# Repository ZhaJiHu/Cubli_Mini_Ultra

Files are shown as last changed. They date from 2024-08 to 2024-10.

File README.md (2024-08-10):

# Cubli_Mini_Ultra项目

**项目完全开源，任何人都可以根据本Github内容自行白嫖，当然也可以顺手点个Star**

## **责任声明：本项目飞轮峰值转速可达到6500RPM，具有一定的危险性，复刻本项目的同学如若发生任何意外，与本人无关**

### 介绍

本项目在Cubli_mini的基础上加上主动刹车，缩小体积。可自动起跳，实现边和点平衡。Cubli_Mini是一个8x8x8CM的立方体，主控集成3路电机驱动、控制、无线射频一体。增加了每个飞轮的外围一圈光污染，主控也增加一条光污染。

项目成本：≤1040RMB

**视频介绍：**[https://www.bilibili.com/video/BV1Gi421D7bc/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](https://www.bilibili.com/video/BV1Gi421D7bc/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)

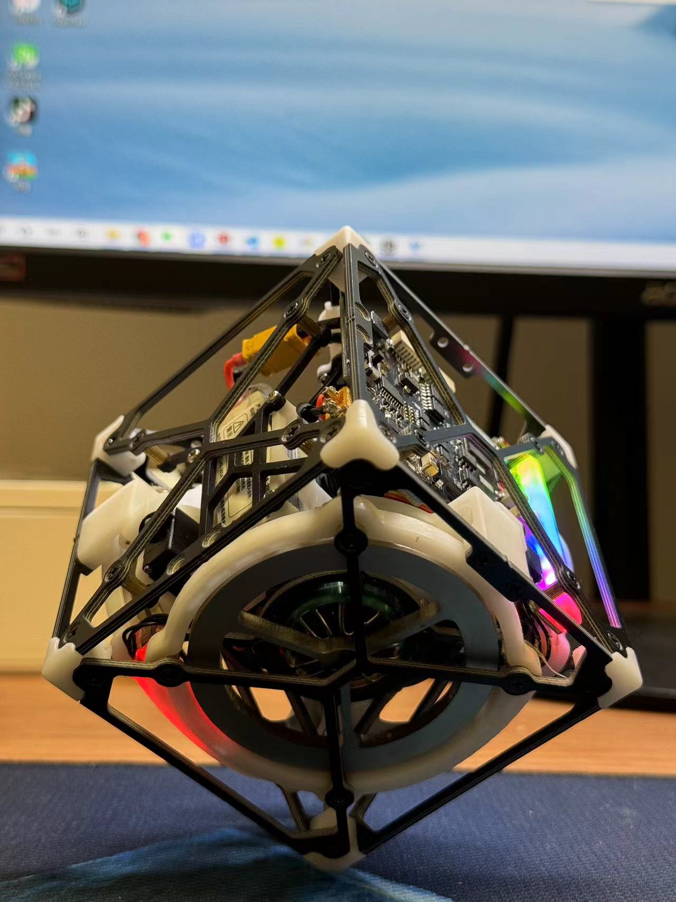
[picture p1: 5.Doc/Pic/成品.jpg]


### 资料说明

- 3D模型设计源文件
- 主控模块、IMU模块、编码器模块、下载模块硬件资料
  - BOM
  - 原理图
  - 位号图
  - Gerber
- 主控1、主控2软件工程
  - 主控模块使用两颗ESP32
- 串口调试助手&简易调参上位机
  - 串口
  - WIFI
- 各类文档说明
  - 对项目的一些说明，如调参，控制原理等
- 打样文件
  - STL格式3D打印文件
  - DWG格式钣金文件
  - BOM表
    - 结构BOM表
    - PCB元器件BOM表

### 结构设计

- 优化了角的结构件设计，通用

- 电池仓、光污染灯罩、刹车底座等使用3D打印文件

- 刹车片使用了70度优力胶聚氨酯板

- 电机安装顺序查看/5.Doc/Pic/电机顺序.png

### 电路模块

**主控模块：**

- 主控使用了单颗ESP32运行3路FOC，使用CAN与另一颗ESP32进行通信，驱动默认使用力矩模式
- FOC使用的Simple FOC，EG2133+6MOS+CC6920SO

**IMU模块：**

- 使用QMI8658A，便宜好用
- 为了防止应力，对IMU所在区域挖槽，减少安装应力。但使用了3颗螺丝硬连接，并不能避免应力问题，改进方案为使用软垫片并只拧紧一个螺丝进一步减少应力
- 为了避免结构干涉，安装与一面进行平行放置，对IMU的数据做旋转矫正

**编码器模块：**

- 采用的是MT6701，便宜好用，转速高

**自动下载模块：**

- 为了尽量减少主控的面积，因此单独把自动下载电路摘出来，参考官方自动下载电路

**注意事项：**

- 正常情况下，自动下载模块焊接排针，主控不焊接任何排针/排母

### 固件说明

MCU2运行3路Simple FOC电机驱动库、以及CAN反馈和接收控制命令

MCU1运行采集IMU，光污染，舵机、控制等任务

**注意事项：**

- 目前WIFI SSID和PSW，TCP Server IP Port全部是写死在固件里面，因此要想使用WIFI调参需要修改这些内容，详情请看Doc/使用和调参说明

### 打样说明

考虑到很多同学可能是第一次进行结构打样，因此提供了打样文件

**3D打印：**

- 文件位于：/6.Process/**3D打印**，该文件为STL格式，打样数量请查看同目录下的<**3D打印加工说明**>，可以在未来工厂或者嘉立创打样，首选光固化

**钣金件打样：**

- 文件位于：/6.Process/**钣金件**，**每个物料的都有对应的PDF和DWG文件，PDF文件方便查看，DWG文件用于激光切割/板材加工**。打样数量请查看同目录下的<**钣金加工说明**>，可以找淘宝给图纸直接加工。由于加工精度要求不高，个人用途下，公差全看加工厂的心情

**PCB打样：**

- 拿着Gerber文件出门左转嘉立创白嫖

**BOM表：**

- PCB BOM文件位于：/1.Hardware/
- 结构BOM文件位于：/6.Process/结构BOM，里面列有需要购买的**结构物料和链接**
- **注意事项：**
  - PCB BOM表是从AD源文件导出，工程会有重复用料，需要注意
  - **注意编码器需要3块，需要采购3套物料**
  - 如文件有遗漏的地方望提醒

### 控制算法

Cubli_Mini使用的是LQR来进行控制，也可以使用串级PID来进行控制。代码位于/需要修改/MCU1/control/cubli_mini

**边平衡**：

- 可以参考一阶倒立摆进行建模和求解参数。由于建立模型的参数比较难准确的获得，我求解得到的参数和最佳参数有些许出入。因此本项目大多数使用玄学调参工程师来整定参数

**点平衡：**

- 在边平衡的基础上添加对X，Z轴的控制。采用与边平衡一样的控制方法，详情看Doc/控制原理说明。

**研究型：**

- 请查看原版Cubli的论文

### 调参

**调节方法：**

- 可以使用UART和WIFI进行调参，WIFI需要连接到路由器，Cubli_Mini_Ultra为TCP客户端

**简易上位机**

- 使用了vofa+进行调参，使用了控件和命令绑定的方式进行调参，保存的文件位于：3.Software/vofa+.tabviews.json
- 只需要使用控件调参拖拽即可，无需了解任何命令

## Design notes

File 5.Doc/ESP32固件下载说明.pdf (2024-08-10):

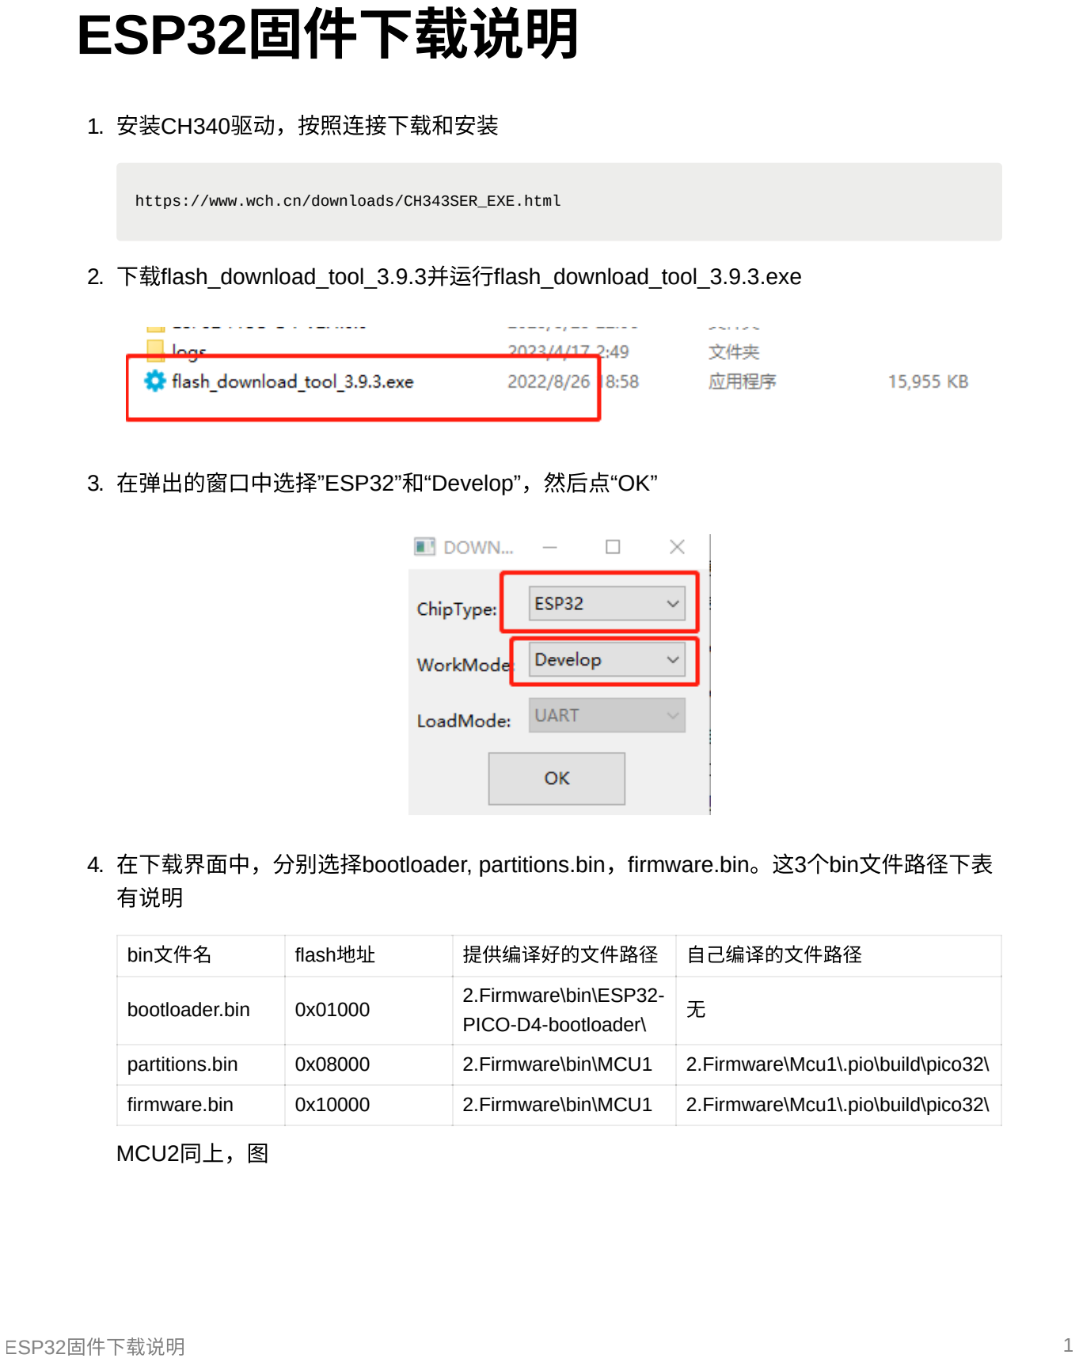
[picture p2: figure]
ESP32固件下载说明; 1. 安装CH340驱动，按照连接下载和安装; https://www.wch.cn/downloads/CH343SER_EXE.html; 3. 在弹出的窗⼝中选择”ESP32”和“Develop”，然后点“OK”; 有说明; bin⽂件名; flash地址; 提供编译好的⽂件路径; ⾃⼰编译的⽂件路径; bootloader.bin; 2.Firmware\bin\ESP32-PICO-D4-bootloader\; partitions.bin; 2.Firmware\bin\MCU1; 2.Firmware\Mcu1\.pio\build\pico32\; firmware.bin; MCU2同上，图

2. 下载flash_download_tool_3.9.3并运⾏flash_download_tool_3.9.3.exe
4. 在下载界⾯中，分别选择bootloader, partitions.bin，firmware.bin。这3个bin⽂件路径下表

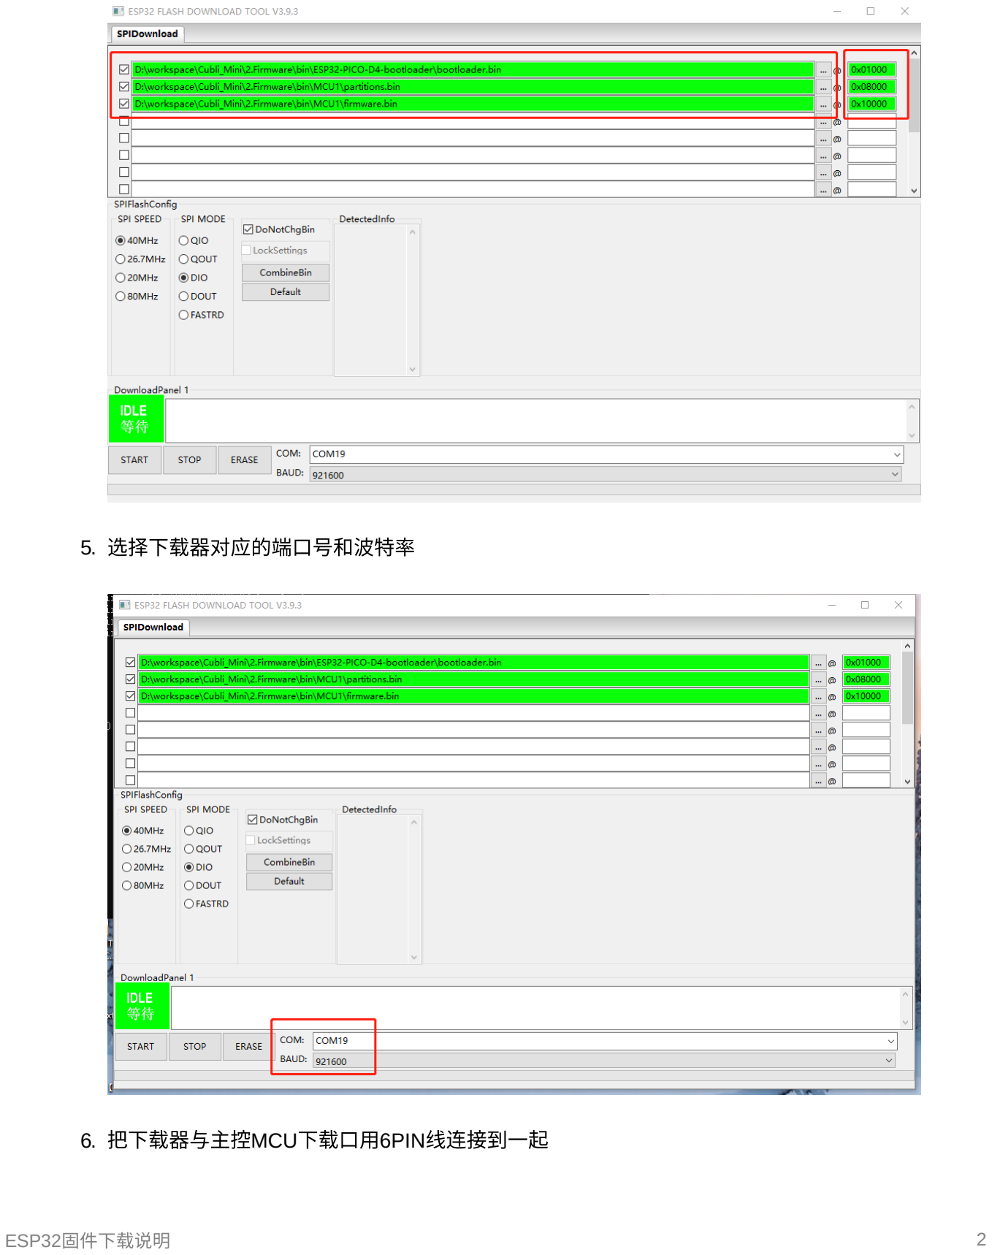
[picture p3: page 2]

5. 选择下载器对应的端⼝号和波特率
6. 把下载器与主控MCU下载⼝⽤6PIN线连接到⼀起

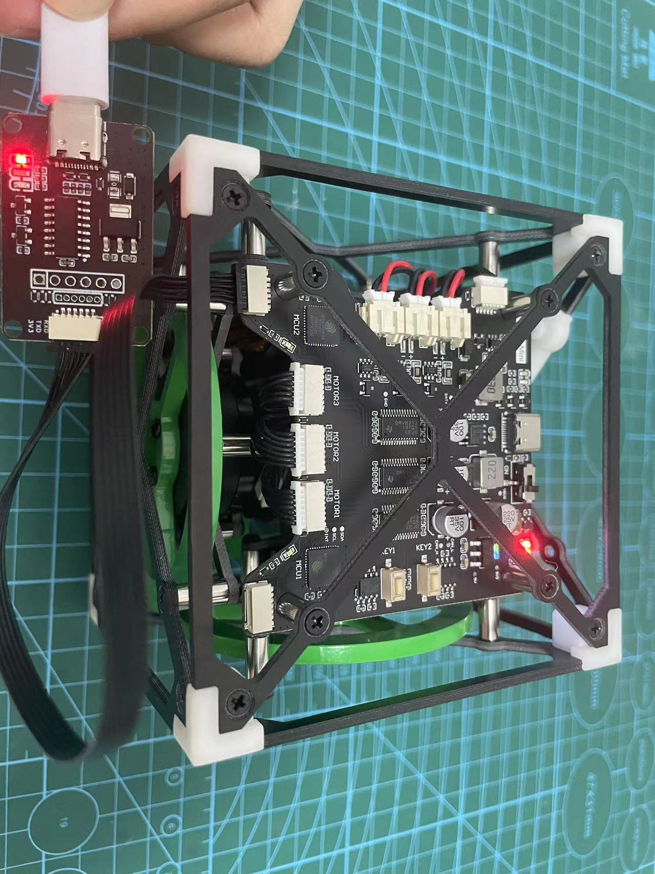
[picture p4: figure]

7. 点下载按钮，等到进度条完成即可下载完成，下载的log也可查看与软件对应⼀起打开的 cmd窗⼝，主控需要下载MCU1和MCU2的固件

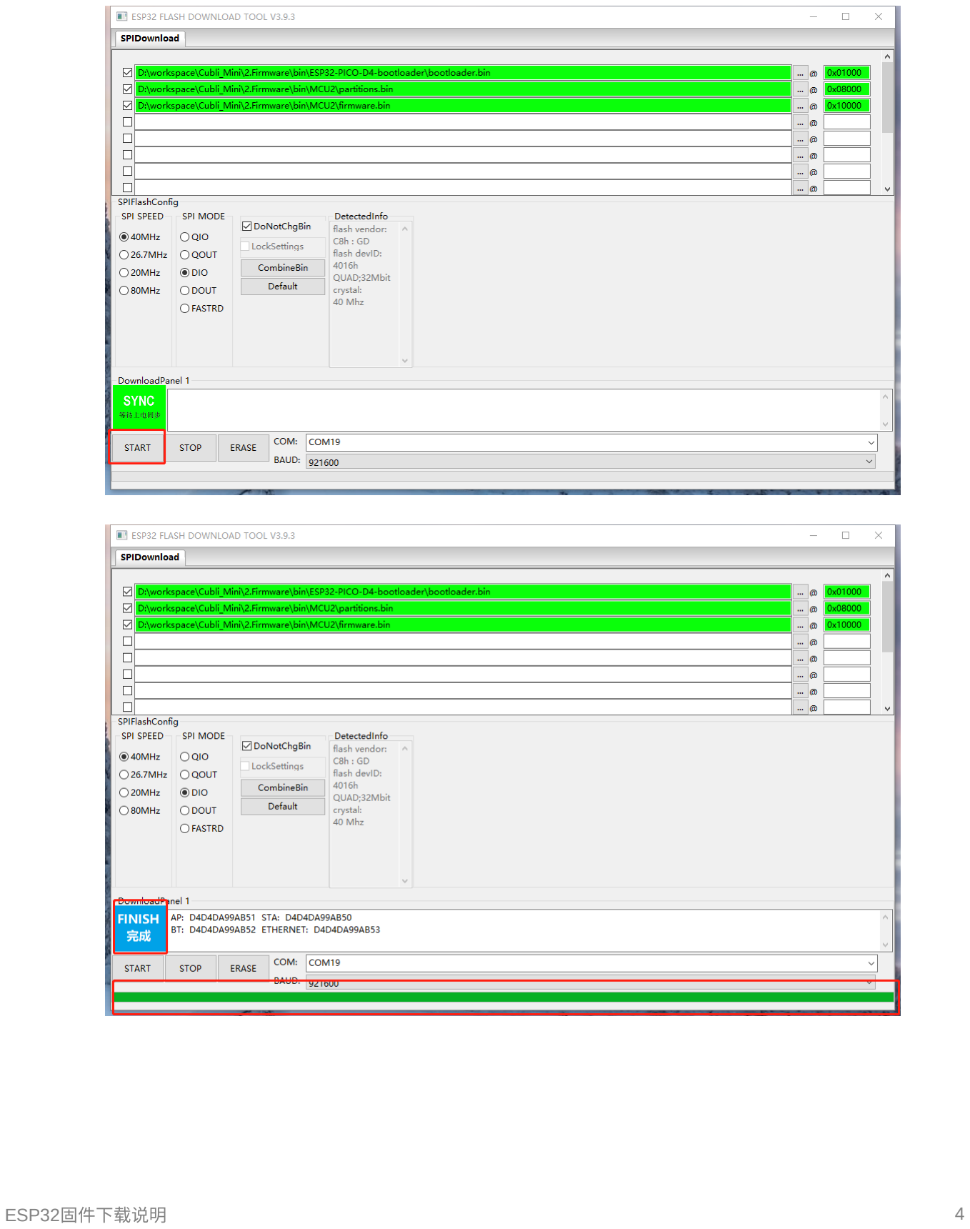
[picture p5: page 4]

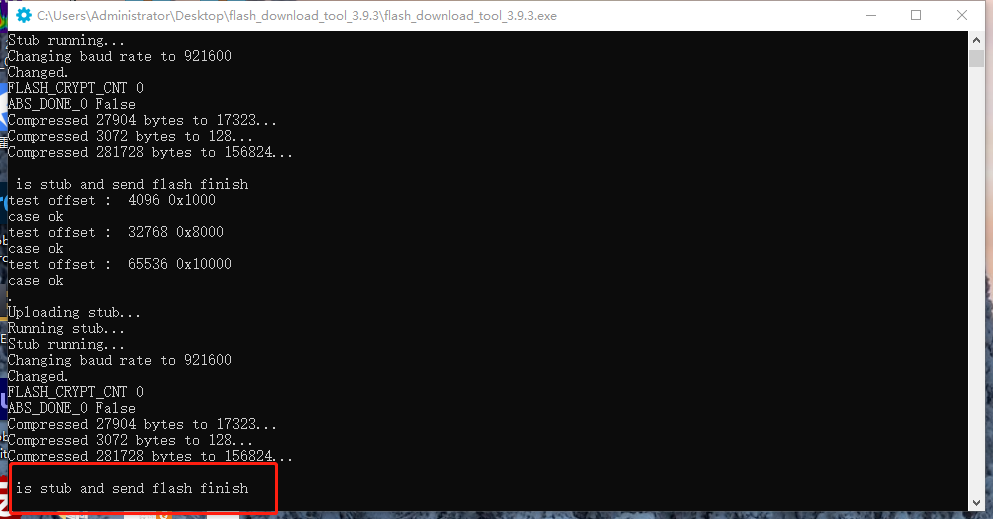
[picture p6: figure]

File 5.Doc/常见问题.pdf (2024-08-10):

常⻅问题 | 1

# 常⻅问题

1. 为什么系统上电初始化需要静置?
a. 原因：IMU零偏问题，IMU需要连续1.5S的时间采集陀螺仪的数据做为零偏，静 置的条件默认需要三轴陀螺仪的读数＜5deg/s（默认，可以在 include/config/config.h中修改阈值），如果IMU的零偏值过⼤，建议更换零偏值 较⼩的IMU
2. 为什么我的IMU模块零偏特别⼤？
a. 安装应⼒，虽然IMU模块把IMU单独挖出来，但是因为上了3颗螺丝，IMU仍然有 可能会受到应⼒的变化，这时候可以通过添加软垫⽚的⽅法解决⼀部分，螺丝尽 量别打太紧，把IMU固定即可
b. IMU IC（mpu6050）原因，IC由于是mems传感器，可能会由于跌落等原因导致 IMU的物理结构受到影响，因⽽导致零偏过⼤，零偏过⼤，不建议使⽤
3. 为什么每个cubli都需要校准平衡的⾓度偏差值？
a. IMU安装之后的轴偏差问题，只讨论轴的所在平⾯是否垂直，不讨论原点是否重 合平⾯的问题
i. 单边平衡问题，结构设计上，处于平衡状态时，IMU反馈的⾓度理论上应该 为0。但是由于⽀点也好，IMU安装件也好都由于误差，会导致在平衡状态 时，IMU的读数不为0，因此需要校准⾓度偏差值

ii. 单点平衡问题同理

4. 为什么我明明已经调参到最佳平衡点了，每次重新上电后总是会发⽣变化，系统不处 于我上次调整的状态？
a. IMU的零偏问题，由于每次IMU上电后零偏会发⽣变化，带来的是融合结果发⽣ 变化，因此体现在动态⾓度上会有些许变化，导致平衡点产⽣偏移，因此上次校 准值不再为最佳参数
b. 解决⽅法
i. 更换性能更好的IMU模块

ii. 采⽤性能更好的IMU融合算法

iii. 对IMU的加速度计和陀螺仪都进⾏校准

常⻅问题 | 2
5. 怎么调整平衡点？
a. 单边情况下，观察动量轮的转动⽅向和转动速度，转动⽅向是与⽅块倾斜⽅向⼀ 致，平衡⾓的偏差⼤⼩决定系统需要的转动惯量，如转动⽅向为顺时针，那么⽅ 块⼀定是往右倾斜，因此需要往反⽅向调节平衡⾓度，调整到动量轮速度⼏乎为 0，这时候就为最佳平衡点
b. 单点情况下，X\Y轴哪个轴倾斜⼤调哪个，调节⽅法同单边
6. 为什么按照默认参数不能⽴起来？
a. 在系统中，控制⾓度θ越⼤，需要的转动惯量也就越⼤。想要更⼤的转动惯量， 要么提⾼动量轮的质量，要么提⾼动量轮的转速。因为所⽤的动量轮质量是恒定 的，所以只能提⾼动量轮的转速。由于所选电机的转速较低，因此很容易达到电 机最⼤转速，失去调节效果，所以⽴⽅体就⽆法再保持平衡。因此需要调整theta ⾓，使得⽴⽅体在转速范围内能提供⾜够的转动惯量去维持⽴⽅体的平衡。

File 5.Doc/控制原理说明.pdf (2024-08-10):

# 控制原理说明

## 单边平衡

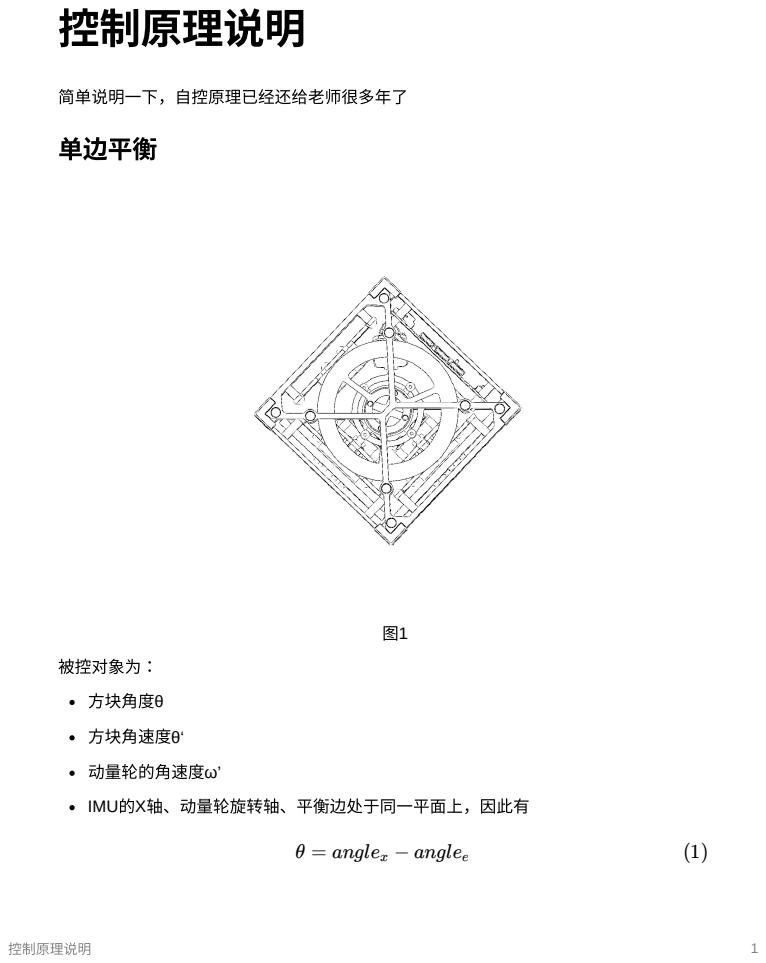
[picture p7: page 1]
控制原理说明; 被控对象为：; ⽅块⾓速度θ‘; 动量轮的⾓速度ω’; θ = anglex − anglee

简单说明⼀下，⾃控原理已经还给⽼师很多年了

IMU的X轴、动量轮旋转轴、平衡边处于同⼀平⾯上，因此有

结合（1）（2）（3）可得

### 参数整定

参数 | 默认数值（默认不 改结构件） | 说明
Kp | -25
Kv | 2
Ks | 0.5
angle_e | 0 | IMU安装误差

## 单点平衡

控制原理为在单边平衡的基础上增加对Y、Z轴的控制

结构如图2所⽰

θ =

′ | gyrox | (2)
ω’ = motorspeedx | (3)
Lqr = (anglex − anglee ) × kp + gyrox × kv + motorspeedx × ks | (4)

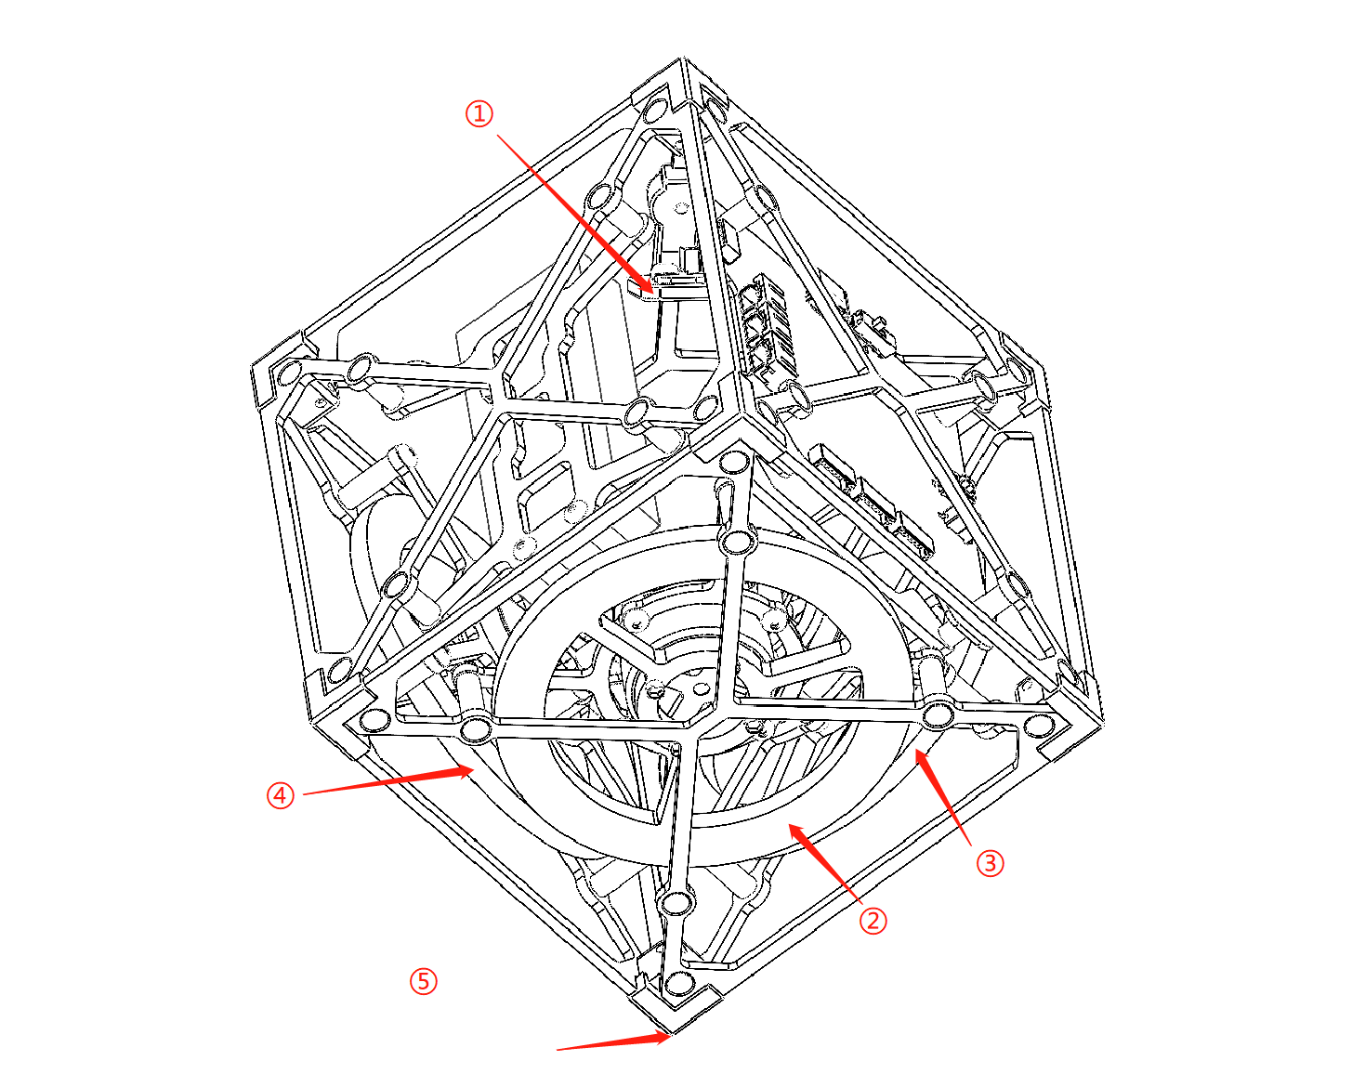
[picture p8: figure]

图2

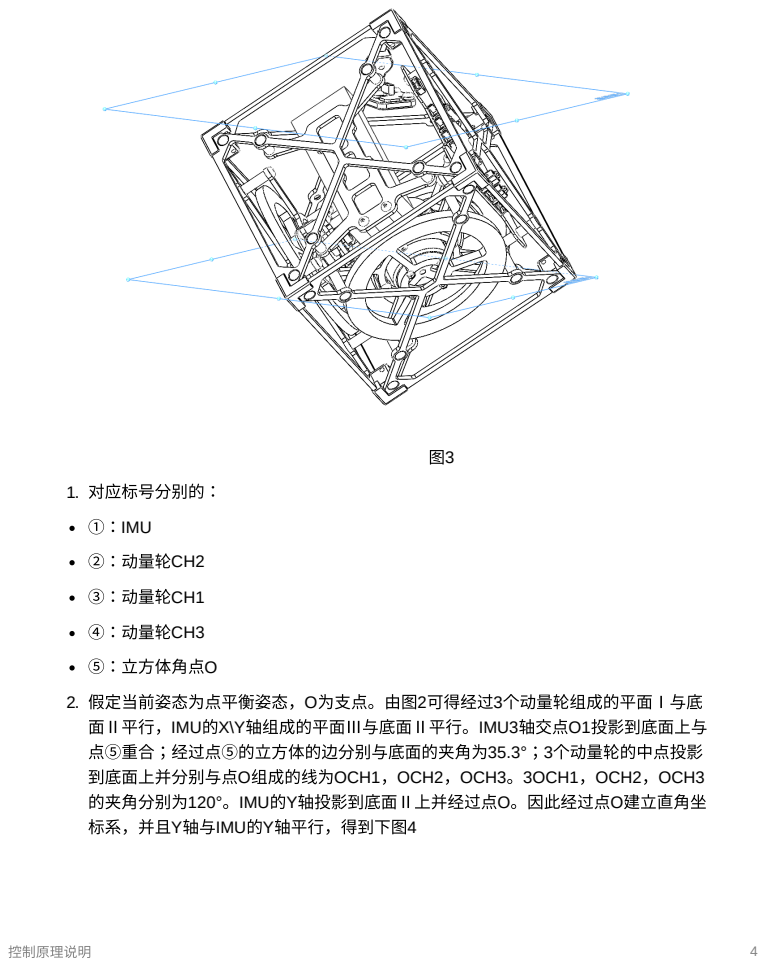
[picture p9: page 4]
1. 对应标号分别的：; ①：IMU; ②：动量轮CH2; ③：动量轮CH1; ④：动量轮CH3

2. 假定当前姿态为点平衡姿态，O为⽀点。由图2可得经过3个动量轮组成的平⾯Ⅰ与底
⾯Ⅱ平⾏，IMU的X\Y轴组成的平⾯Ⅲ与底⾯Ⅱ平⾏。IMU3轴交点O1投影到底⾯上与
点⑤重合；经过点⑤的⽴⽅体的边分别与底⾯的夹⾓为35.3°；3个动量轮的中点投影
到底⾯上并分别与点O组成的线为OCH1，OCH2，OCH3。3OCH1，OCH2，OCH3
的夹⾓分别为120°。IMU的Y轴投影到底⾯Ⅱ上并经过点O。因此经过点O建⽴直⾓坐
标系，并且Y轴与IMU的Y轴平⾏，得到下图4

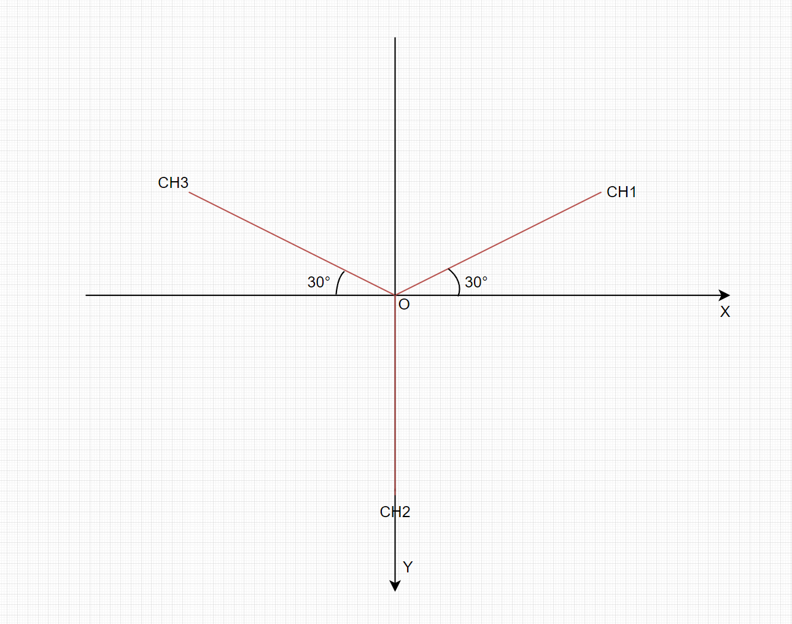
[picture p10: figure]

图4

3. 动量轮CH1\CH2\CH3的转动速度⽅向与OCH1\OCH2\OCH3垂直，因此分别平⾏移 动到经过点0后可以得到下图

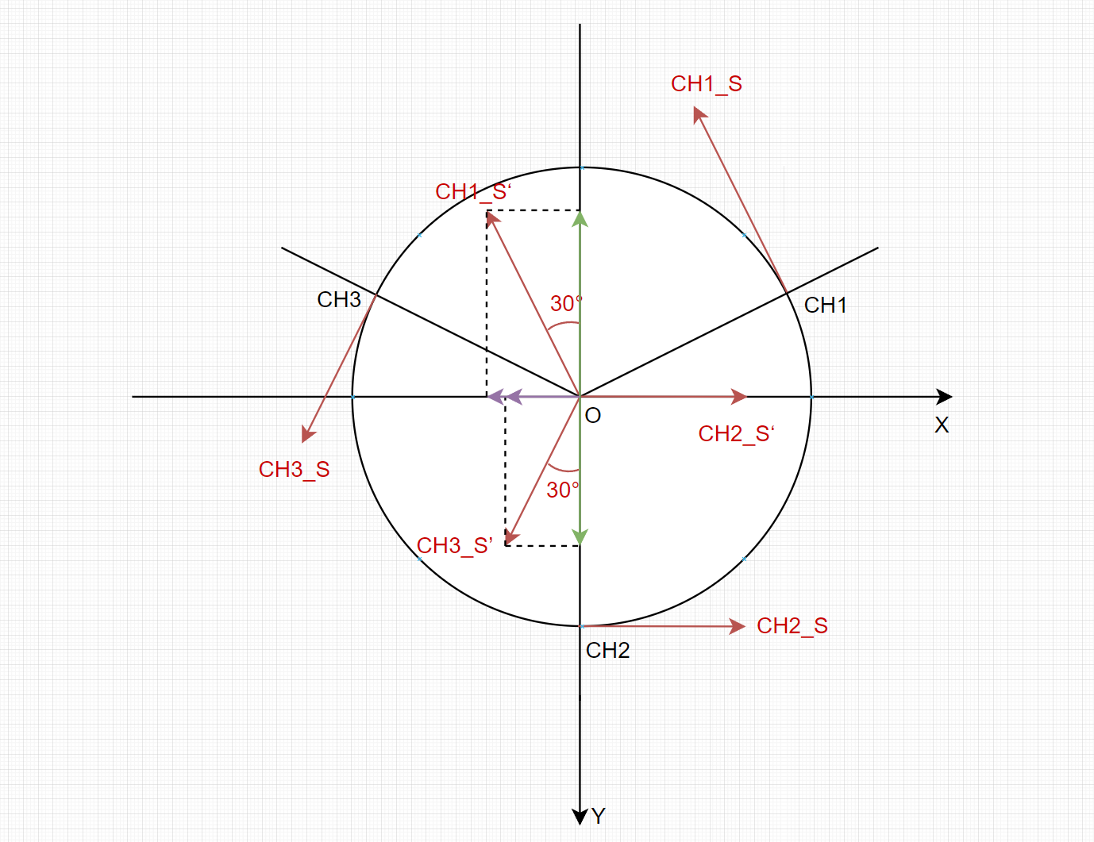
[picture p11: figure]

图5

由图5的关系可以得到（4）（5）（6）

根据单边控制⽅法分别控制X，Y，Z轴，可得（7）（8）（9）

sx = sch2 − sch1 × sin(30°) − sch3 × sin(30°) | (4)
sy = sch3 × cos(30°) − sch1 × cos(30°) | (5)
sz = sch1 + sch2 + sch3 | (6)
Lx = (anglex − anglexe ) × kxp + gyrox × kxv + sx × kxs | (7)
Ly = (angley − angleye ) × kyp + gyroy × kyv + sy × kys | (8)
Lz = (anglez − angleye ) × kzp + gyroz × kzv + sz × kzs | (9)

由图6可得（10）（11）（12）

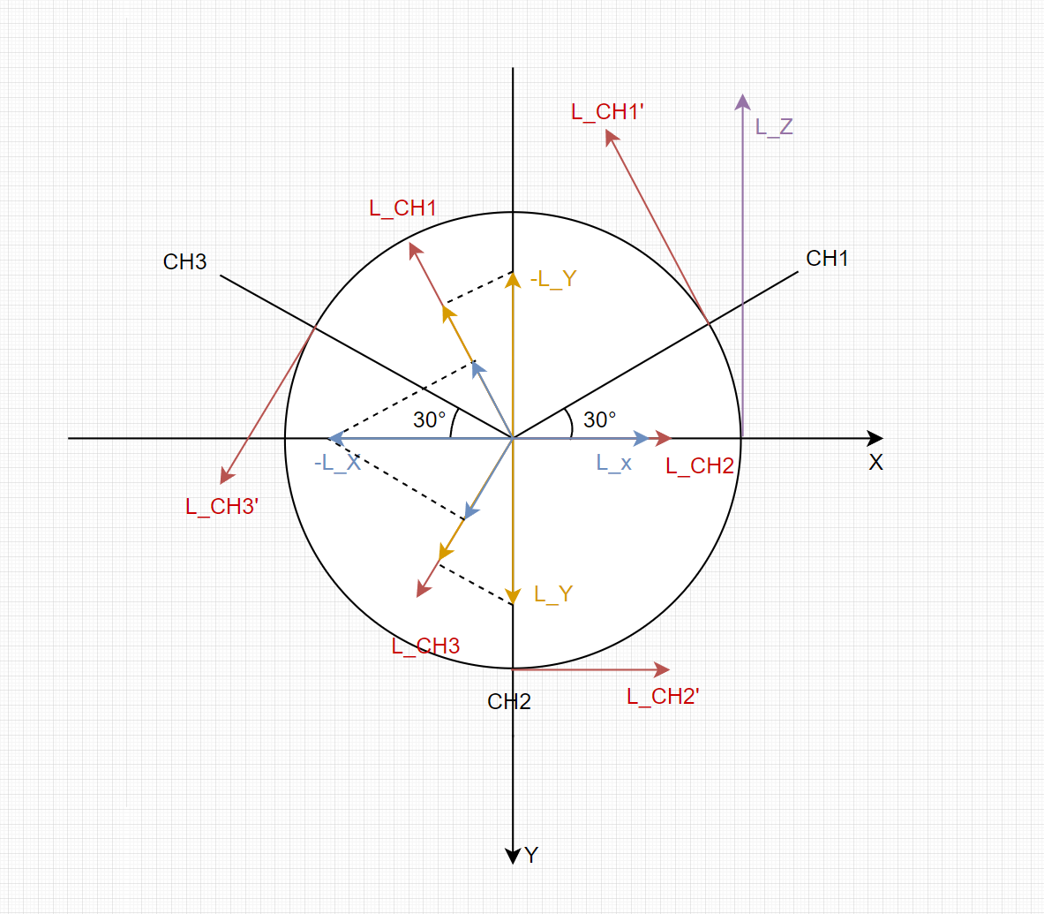
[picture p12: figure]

图6

### 参数整定

## Sch1 = −Ly × cos(30°) − Lx × sin(30°) +

3

Lz
(10)

Sch2 = Lx +
3

Lz
(11)

## Sch3 = Ly × cos(30°) − Lx × sin(30°) +

3

Lz
(12)

参数 参数 | 默认数值（默认 默认数值（默认 不改结构，⽞学 不改结构，⽞学 调参） 调参） | 说明 说明
Kxp | -17
Kxv | 1.5
Kxs | 0.3
angle_xe | 0.5 | IMU安装误差
Kyp | 18
Kyv | 1.6
Kys | 0.3
angle_ye | 1.5
Kzp | 0 | IMU安装误差
Kzv | -0.3
Kzs | 0.02
angle_ze | 0 | 默认不对Z轴⾓度控制，IMU 的Z轴会因为零偏漂移

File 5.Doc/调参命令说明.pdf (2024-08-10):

调参命令说明 | 1

# 调参命令说明

## 结构说明

①②③.....data\r\n（字符串形式）

## 命令说明

获取参数 | 说明
GP | 获取单点平衡的参数
GU | 获取单边平衡的参数
GA | 获取点平衡模式⾓度数据（10hz刷新）

设置单点平衡参数

SPXP（data） | x轴的Kp参数，如SPXP3，Kp为3，data∈（-float, +float）
SPXV（data） | x轴的Kv参数，如SPXV3，Kv为3
SPXS（data） | x轴的Ks参数，如SPXS3，Ks为3
SPXA（data） | x轴的平衡⾓度参数，如SPXA3，平衡⾓度为3
SPYP（data） | y轴的Kp参数，如SPYP3，Kp为3
SPYV（data） | y轴的Kv参数，如SPYV3，Kv为3
SPYS（data） | y轴的Ks参数，如SPYS3，Ks为3
SPYA（data） | y轴的平衡⾓度参数，如SPYA3，平衡⾓度为3
SPZP（data） | z轴的Kp参数，如SPZP3，Kp为3
SPZV（data） | z轴的Kv参数，如SPZV3，Kp为3
SPZS（data） | z轴的Ks参数，如SPZS3，Ks为3
SPZA（data） | z 轴的平衡⾓度参数，如SPZA3，平衡⾓度为3
SPA（data） | 不使⽤

设置单边平衡参数

SUP（data) | Kp参数，如SUP3，Kp为3
SUV（data) | Kv参数，如SUV3，Kvp为3
SUS（data) | Ks参数，如SUS3，Ks为3

获取参数 | 说明
SUA（data) | 平衡⾓度参数，如SUA3，平衡⾓度为3

保存参数

SSP | 保存单点平衡参数
SSU | 保存单边平衡参数

## 命令详情

## 获取命令

结构：①②data\r\n

1. ①
a. G：获取
2. ②
a. P：单点平衡数据参数（只返回⼀次）
b. U：单边平衡参数（只返回⼀次）
c. A：⾓度数据（持续推送，推送三轴⾓度）
3. 如：
a. GP：获取单点平衡的参数
b. GU：获取单边平衡的参数
c. GA：获取⾓度数据（10hz刷新）

## 设置命令

结构为：①②③④.....data\r\n

1. ①
a. S：命令
2. ②

P：代表单点平衡参数

U：代表单边平衡参数

S：保存参数

## 单点平衡参数

结构为：①②③④data\r\n

1. ③
a. X：代表X轴
b. Y：代表Y轴
c. Z：代表Z轴
d. A：不使⽤
2. ④
a. P：代表⾓度kp参数
b. V：代表⾓速度kv参数
c. S：代表动量轮速度ks参数
d. A：代表⾓度偏差值
3. 如：
a. SPXP3 代表X轴⾓度参数kp为3
b. SPYV3 代表Y轴⾓度参数kv为3
c. SPZS3 代表Z轴动量轮速度ks为3
d. SPXA3 代表X轴⾓度偏差值为3°

## 单边平衡参数（只写了电机2）

结构为：①②③data\r\n

1. ③
a. P：代表⾓度参数Kp
b. V：代表⾓速度参数Kv
c. S：代表⻜轮速度参数Ks
d. A：代表⾓度偏差值

2. 如：
a. SUP3 代表⾓度参数Kp为3
b. SUV3 代表⾓度参数Kv为3
c. SUS3 代表动量轮速度Ks为3
d. SUA3 代表⾓度偏差值为3°

## 保存参数

结构为：①②③data\r\n

1. ③
a. P：代表单点平衡参数
b. U：代表单边平衡参数
2. 如：
a. SSP：保存单点的参数
b. SSU：保存单边的参数

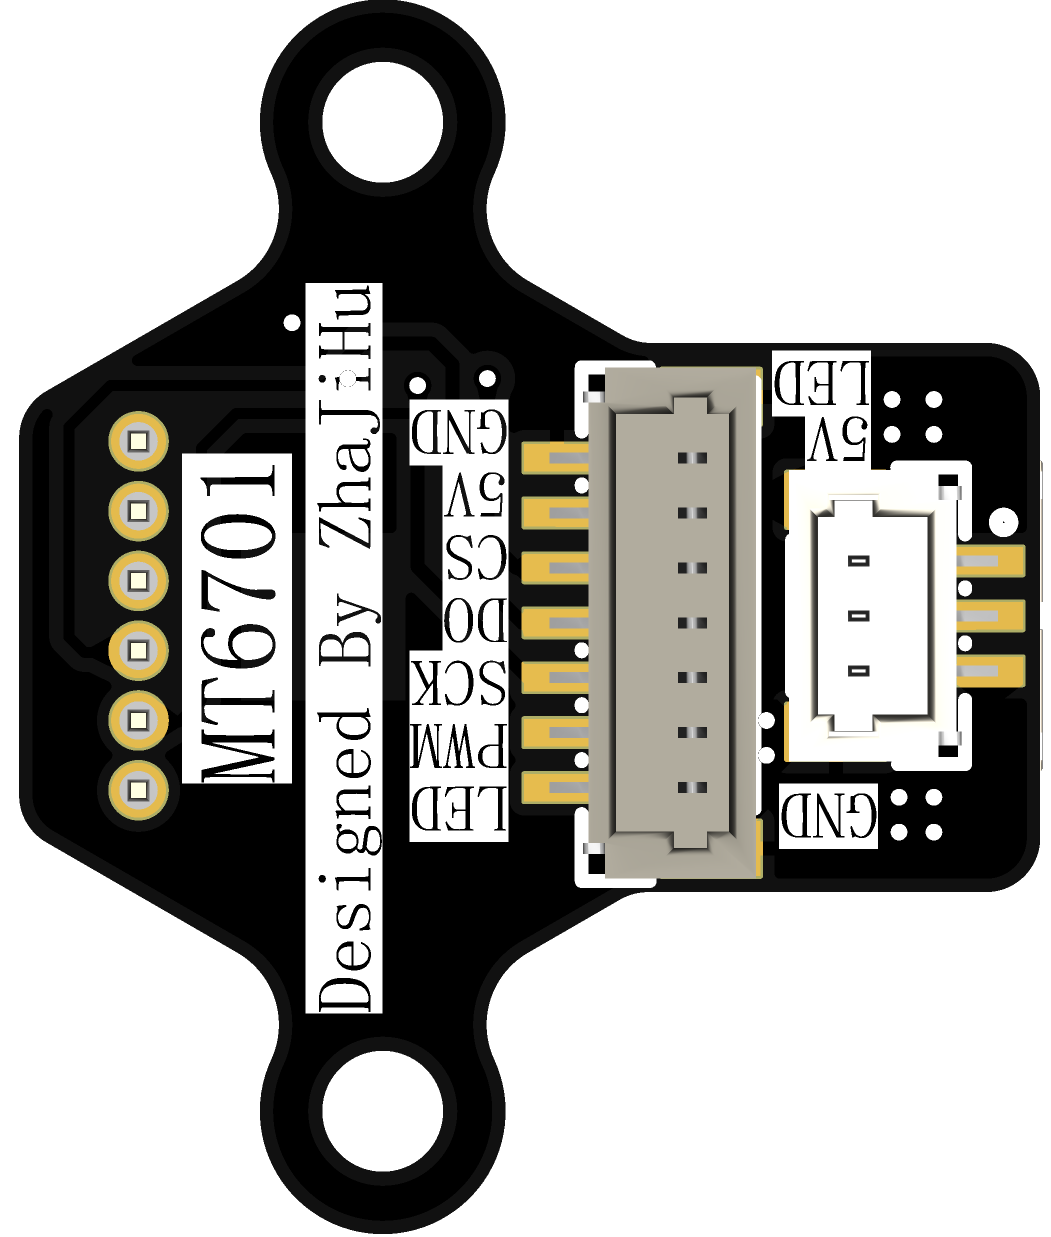
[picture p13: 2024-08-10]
5.Doc/Pic/编码器反.png

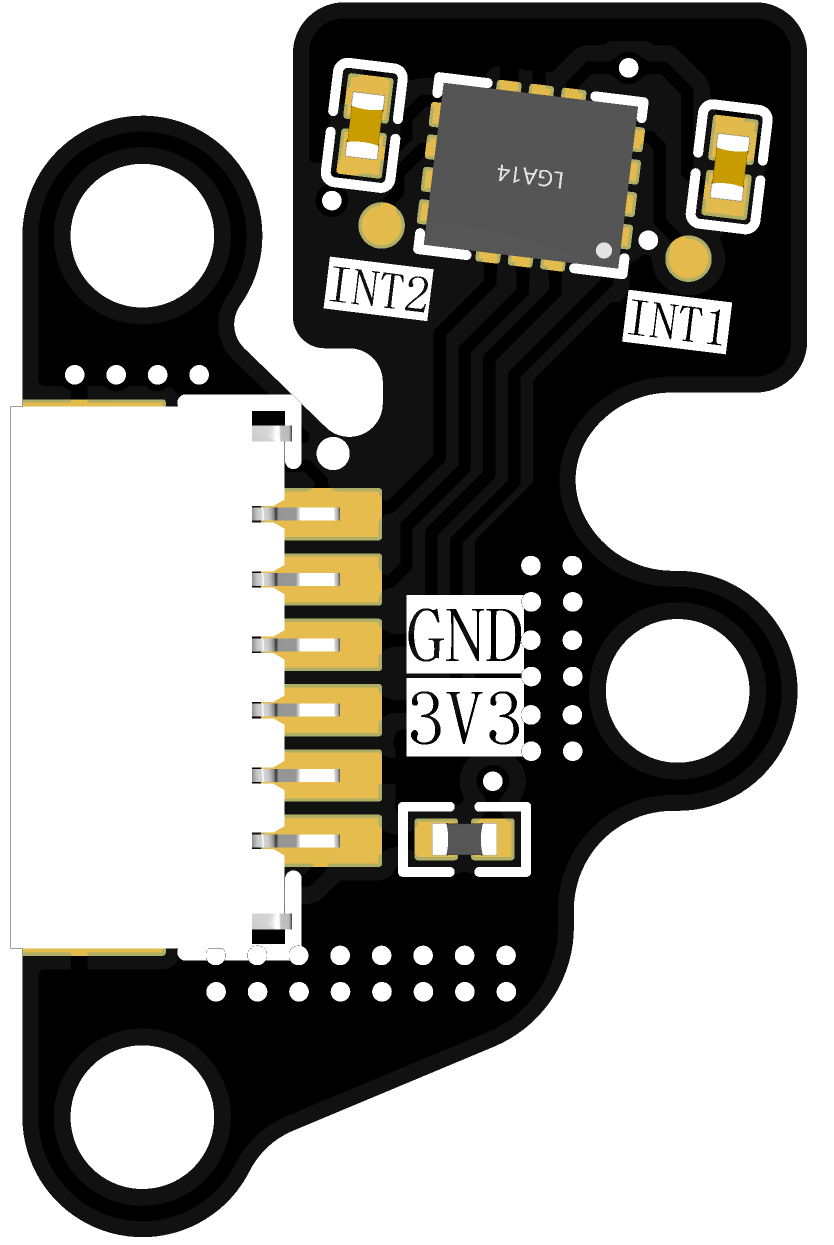
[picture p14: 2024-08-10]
5.Doc/Pic/IMU板.png

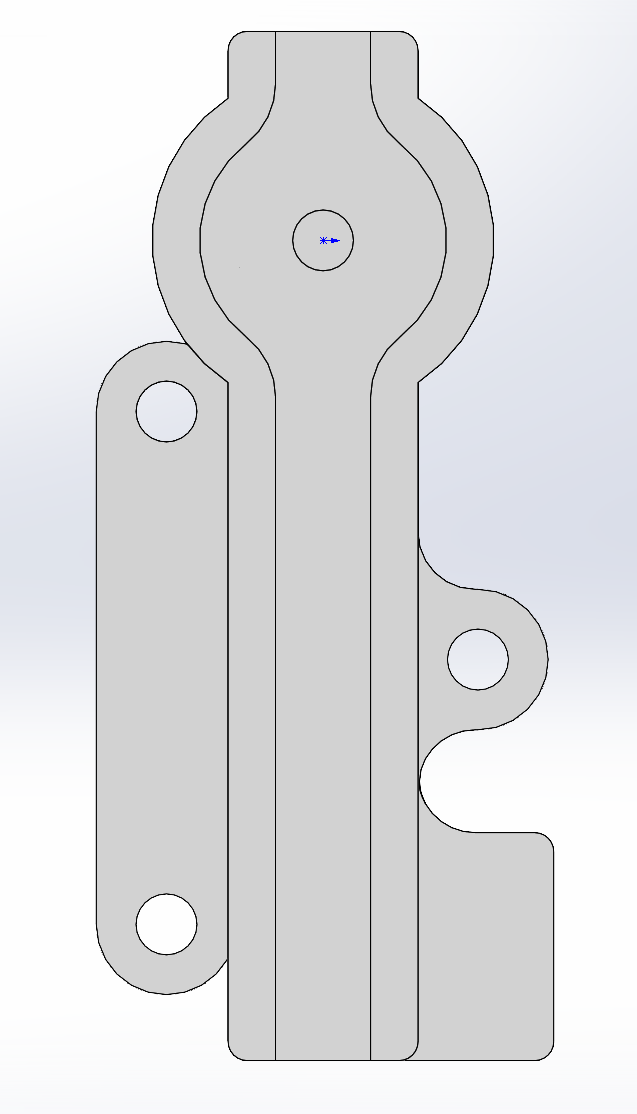
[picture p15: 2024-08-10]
5.Doc/Pic/IMU安装座.png

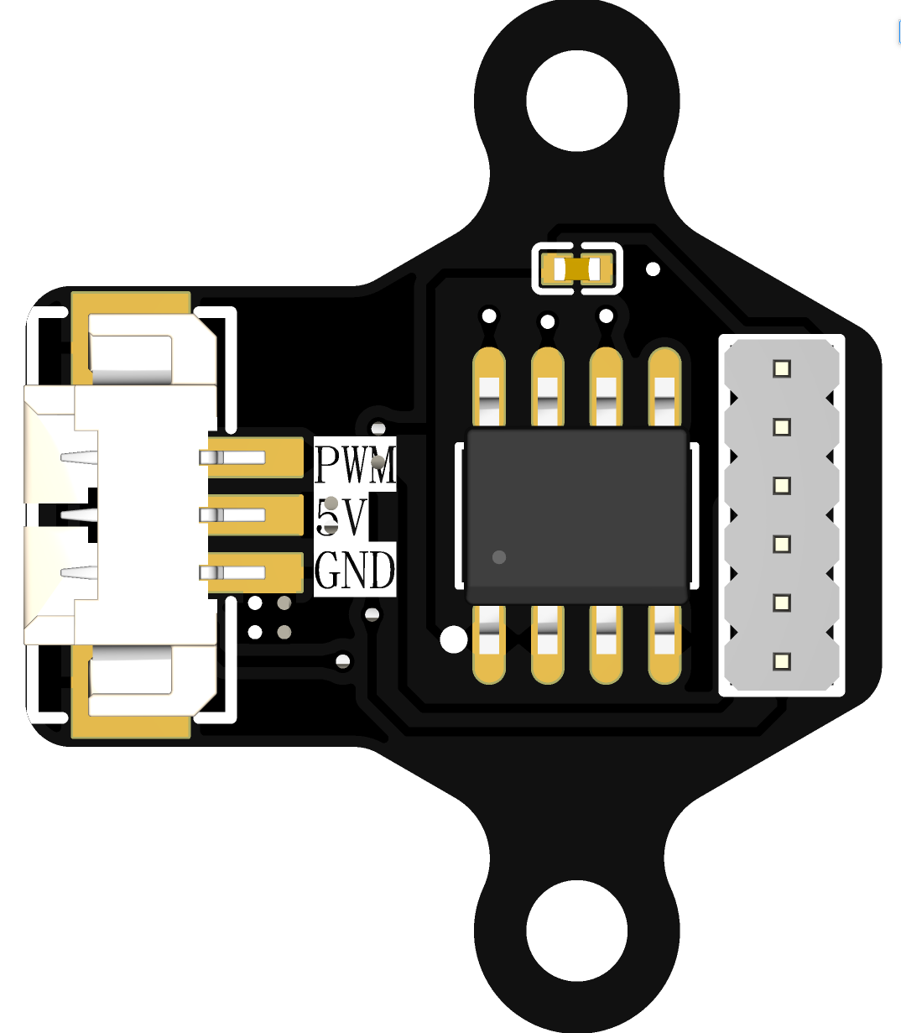
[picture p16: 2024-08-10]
5.Doc/Pic/编码器正.png

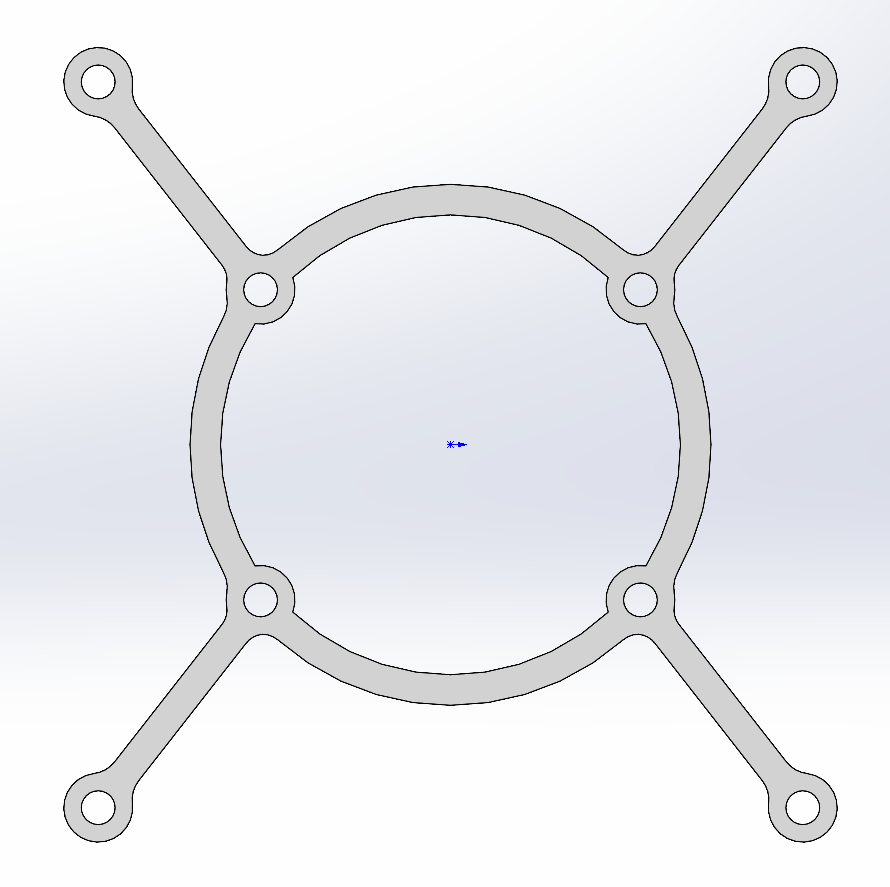
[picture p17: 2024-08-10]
5.Doc/Pic/电机连接框.png

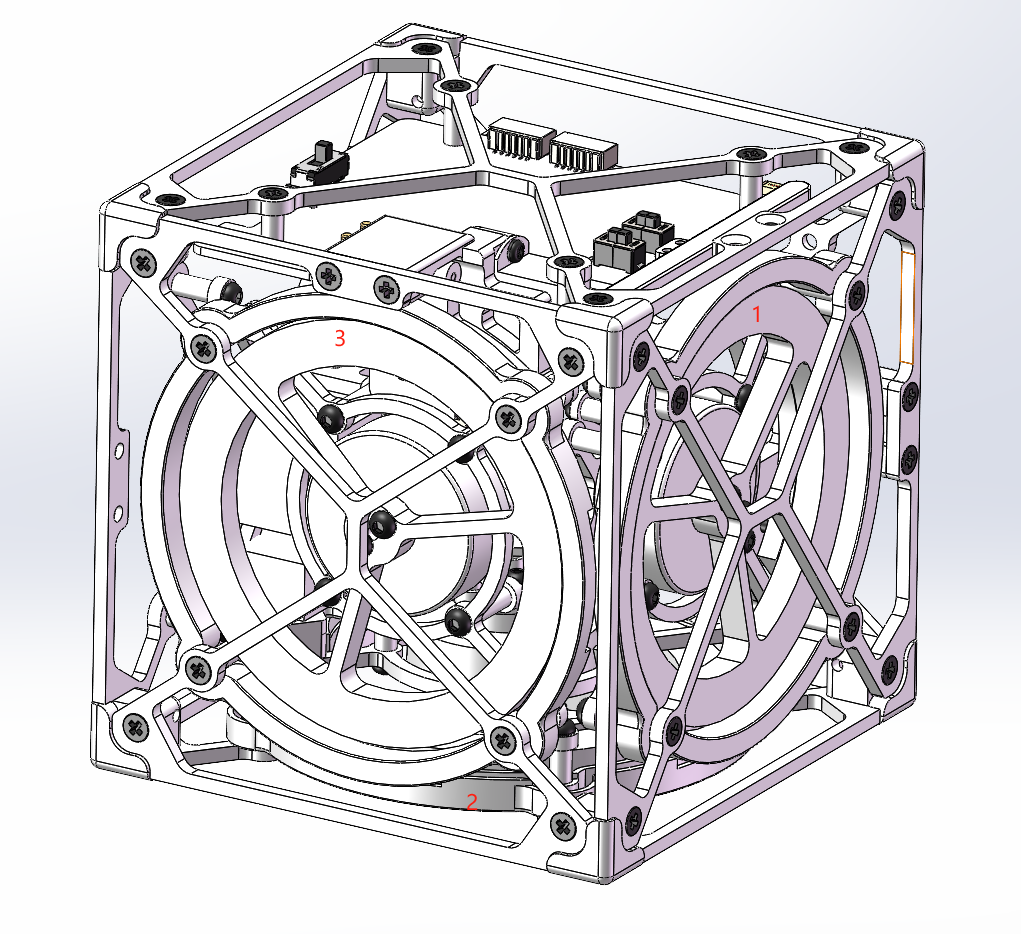
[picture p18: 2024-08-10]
5.Doc/Pic/电机顺序.png

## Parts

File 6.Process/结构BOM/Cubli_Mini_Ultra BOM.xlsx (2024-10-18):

缩略图 | 零件号 | 说明 | 数量 | 单价 | 总价 | 链接
 | 飞轮_2004 | 4MM 304不锈钢 喷砂 120目 | 3 | 15 | 45 | 嘉立创钣金加工
 | 外框001 | 2MM 玻纤加工 | 6 |  | 120 | https://szyifeng.taobao.com/shop/view_shop.htm?user_number_id=911417640
 | 外框003.3.2004 | 2MM 玻纤加工 | 3
 | 外框002.2.2004 | 2MM 玻纤加工 | 3
 | M2_滚花黄铜柱X6MM |  | 8 | 0.06 | 0.48 | https://detail.tmall.com/item.htm?id=598149908477&_u=s1jbj7pb2948&skuId=4172330993466
 | M2_滚花黄铜柱x4mm |  | 6 | 0.06 | 0.36 | https://detail.tmall.com/item.htm?id=598149908477&_u=s1jbj7pb2948&skuId=4172330993467
 | M2_滚花黄铜柱_9MM |  | 24 | 0.08 | 1.92 | https://detail.tmall.com/item.htm?id=598149908477&_u=s1jbj7pb2948&skuId=4172330993472
 | IMU底座-平面 | 3D打印 | 1 | 2 | 2 | 嘉立创3维猴
 | 电池安装座 | 3D打印 | 1 | 2 | 2
 | 电池安装座001 | 3D打印 | 1 | 2 | 2
 | 主控灯罩 | 3D打印 | 1 | 2 | 2
 | 舵机安装座 | 3D打印 | 3 | 2 | 6
 | 角001 | 3D打印 | 8 | 2 | 16
 | 刹车片安装座 | 3D打印 | 3 | 2 | 6
 | 舵机-舵臂-加强_8mm | 3D打印 | 3 | 2 | 6
 | 角度标定台(可选) | 3D打印 | 1 | 6 | 6
 | 飞轮灯罩（可选） | 3D打印 | 3 | 3 | 9
 | 2g舵机 |  | 3 | 14 | 42 | https://item.taobao.com/item.htm?id=820138968539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
 | 刹车片-1 | 聚氨酯 70度 | 3 | 0 | 100 | https://item.taobao.com/item.htm?id=708052153883&_u=s1jbj7pba4ec&skuId=5142662030325
 | 沉头十字螺丝_M2 X 5mm_L包含头部 |  | 20 |  | 3.92 | https://detail.tmall.com/item.htm?id=634410753197&spm=a1z09.2.0.0.13f22e8dqgtkgC&_u=s1jbj7pb33da
 | 沉头平尾十字自攻螺丝_M2 X L5mm_L包含头部 |  | 32 |  | 4.4 | https://detail.tmall.com/item.htm?id=608693213885&spm=a1z09.2.0.0.13f22e8dqgtkgC&_u=s1jbj7pb6f9c
 | 圆头内六角螺丝_M2 X 6mm_L不包含头部 |  | 22 |  | 4.69 | https://detail.tmall.com/item.htm?id=16979965616&spm=a1z09.2.0.0.13f22e8dqgtkgC&_u=s1jbj7pb08af
 | 圆头内六角螺丝_M2 X 4mm_L不包含头部 |  | 22 |  | 4.52 | https://detail.tmall.com/item.htm?id=16979965616&spm=a1z09.2.0.0.13f22e8dqgtkgC&_u=s1jbj7pb08af
 | 圆头内六角螺丝_M2 X 3 mm_L不包含头部 |  | 10 |  | 4.52 | https://detail.tmall.com/item.htm?id=16979965616&spm=a1z09.2.0.0.13f22e8dqgtkgC&_u=s1jbj7pb08af
 | 圆头平尾十字自攻螺丝_M1.7 X 4mm_L不包含头部 |  | 18 |  | 3.52 | https://detail.tmall.com/item.htm?id=21325368367&spm=a1z09.2.0.0.13f22e8dqgtkgC&_u=s1jbj7pb2530
 | 圆头平尾十字自攻螺丝_M2 X 3mm_L不包含头部 |  | 6 |  | 4.08 | https://detail.tmall.com/item.htm?id=21325368367&spm=a1z09.2.0.0.13f22e8dqgtkgC&_u=s1jbj7pb2530
 | 2004电机 KV1800(6S) |  | 3 | 48.37 | 145.11 | https://item.taobao.com/item.htm?id=696547975526&_u=s1jbj7pb6d0f&sku_properties=31309:2428317975
 | D3.3xD2x2_径向磁铁 |  | 3 | 1.98 | 5.94 | https://detail.tmall.com/item.htm?id=558323628941&spm=a1z09.2.0.0.13f22e8dqgtkgC&_u=s1jbj7pbf8f2
 | 格式3S_300mAh电池 |  | 1 | 46.12 | 46.12 | https://item.taobao.com/item.htm?id=649736883091&_u=s1jbj7pb2fd0&skuId=4853734987014
 | 主控_PCB |  | 1 | 250 | 250 | 嘉立创
 | IMU_PCB |  | 1 | 20 | 20
 | 编码器PCB |  | 3 | 18 | 54
 | 下载器PCB |  | 1 | 20 | 20
 | SH1.0MM双头 7P 100mm | 反向 | 3 | 0.82 | 2.46 | https://item.taobao.com/item.htm?id=581255230378&_u=s1jbj7pb9e3c&skuId=5220929082860
 | SH1.0MM双头 6P 50mm | 反向 | 1 | 0.84 | 0.84 | https://item.taobao.com/item.htm?id=581255230378&_u=s1jbj7pb9e3c&skuId=5220929082831
 | SH1.0MM双头 6P 300mm | 反向 | 1 | 1.2 | 1.2 | https://item.taobao.com/item.htm?id=581255230378&_u=s1jbj7pb9e3c&skuId=5220929082816
 | PH2.0接插件 胶壳 端子 | 胶壳 端子 压线用 | 1 | 3.28 | 3.28 | https://detail.tmall.com/item.htm?id=622922160512&_u=s1jbj7pbab96&skuId=4582039771546
 | 压线钳SN-01BM（可选） | 压线用 | 1 | 65 | 65 | https://detail.tmall.com/item.htm?id=623774373198&_u=s1jbj7pbd079&skuId=4460140936012
 | B3简易平衡充 | 锂电池充电 | 1 | 21.34 | 21.34 | https://item.taobao.com/item.htm?id=538620371117&_u=s1jbj7pb66a6&sku_properties=1627207:1510157416
 | XT30 公母头一对 | 电池延长线用 | 1 | 3.08 | 3.08 | https://item.taobao.com/item.htm?id=598239222968&_u=s1jbj7pb411d&skuId=4812197836030
 | 22AWG 硅胶线 | 红+黑 1m | 2 | 0.59 | 1.18 | https://item.taobao.com/item.htm?spm=a1z09.2.0.0.46b02e8dvYqOsU&id=578808837427&_u=s1jbj7pb83aa
 | 细小扭簧 | 外径 圈数 角度（2 6 240） | 1 | 9.8 | 9.8 | https://item.taobao.com/item.htm?id=628461434349&_u=v1jbj7pb47cc&skuId=4458233812334
 | 304不锈钢柱 | 1X14MM | 3 | 1.24 | 1.24 | https://detail.tmall.com/item.htm?id=682759723938&_u=a1jbj7pbf2ff&skuId=5058337319770
 | 2.6mm光污染灯条 | 5V-2.6mm 750MM长-100灯 | 1 | 31.5 | 27.6 | https://item.taobao.com/item.htm?_u=i1jbj7pb114c&id=724934408746&skuId=5205478106341
 |  |  |  |  | 1074.6

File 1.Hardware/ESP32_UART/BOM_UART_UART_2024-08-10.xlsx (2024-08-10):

No. | Quantity | Comment | Designator | Footprint | Value | Manufacturer Part | Manufacturer | Supplier Part | Supplier
1 | 2 | 10uF | C7,C8 | C0402 | 10uF | CL05A106MQ5NUNC | SAMSUNG(三星) | C15525 | LCSC
2 | 1 | 100nF | C9 | C0402 | 100nF | CL05B104KB54PNC | SAMSUNG(三星) | C307331 | LCSC
3 | 1 | HC-1.0-6PWT | CN1 | CONN-SMD_HCTL_HC-1.0-6PWT |  | HC-1.0-6PWT | HCTL(华灿天禄) | C2845365 | LCSC
4 | 1 | 1N5819W | D13 | SOD-123_L2.8-W1.8-LS3.7-RD |  | 1N5819W | TWGMC(台湾迪嘉) | C727115 | LCSC
5 | 3 | LESD5D5.0CT1G | D14,D15,D16 | SOD-523_L1.2-W0.8-LS1.6-BI |  | LESD5D5.0CT1G | LRC(乐山无线电) | C383211 | LCSC
6 | 5 | ESD5Z3.3C | D17,D18,D19,D20,D21 | SOD-523_L1.2-W0.8-LS1.6-BI |  | ESD5Z3.3C | MDD | C502551 | LCSC
7 | 1 | BSMD0805-110-6V | F2 | F0805 |  | BSMD0805-110-6V | BHFUSE(佰宏) | C883113 | LCSC
8 | 1 | KH-1.27PH180-1X6P-L7.2 | H1 | HDR-TH_6P-P1.27-V-M-A |  | KH-1.27PH180-1X6P-L7.2 | kinghelm(金航标) | C2938402 | LCSC
9 | 1 | Z-211-0611-0021-001 | H2 | HDR-TH_6P-P2.54-V_Z-211-0611-0021-001 |  | Z-211-0611-0021-001 | Nextron(正凌) | C190819 | LCSC
10 | 2 | TLMS1000-GS08 | LED4,LED5 | LED0603-R-RD |  | TLMS1000-GS08 | VISHAY(威世) | C241893 | LCSC
11 | 2 | SS8050 | Q3,Q4 | SOT-23-3_L2.9-W1.3-P1.90-LS2.4-BR |  | SS8050 | CJ(江苏长电/长晶) | C2150 | LCSC
12 | 2 | 5.1kΩ | R12,R13 | R0402 | 5.1kΩ | RC0402FR-075K1L | YAGEO(国巨) | C105872 | LCSC
13 | 2 | 100Ω | R14,R15 | R0402 | 100Ω | RC0402FR-07100RL | YAGEO(国巨) | C106232 | LCSC
14 | 3 | 1kΩ | R16,R17,R18 | R0402 | 1kΩ | ERA2AEB102X | PANASONIC(松下) | C445596 | LCSC
15 | 2 | 10kΩ | R19,R20 | R0402 | 10kΩ | 0402WGF1002TCE | UNI-ROYAL(厚声) | C25744 | LCSC
16 | 1 | AMS1117-3.3 | U3 | SOT-223-4_L6.5-W3.5-P2.30-LS7.0-BR |  | AMS1117-3.3 | UMW(广东友台半导体) | C347222 | LCSC
17 | 1 | CH340C | U4 | SOP-16_L10.0-W3.9-P1.27-LS6.0-BL |  | CH340C | WCH(南京沁恒) | C84681 | LCSC
18 | 1 | 19-21/G6C-FM1N2B/4T | U5 | LED0603-R-RD_GREEN |  | 19-21/G6C-FM1N2B/4T | EVERLIGHT(亿光) | C2984263 | LCSC
19 | 1 | KH-TYPE-C-16P | USB2 | USB-C-SMD_KH-TYPE-C-16P |  | KH-TYPE-C-16P | kinghelm(金航标) | C709357 | LCSC

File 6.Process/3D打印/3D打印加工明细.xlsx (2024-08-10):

名称 | 数量
IMU底座-平面 | 1
电池安装座001 | 1
电池安装座002 | 1
舵机安装座 | 3
刹车片安装座 | 3
舵机-舵臂-加强 | 3
飞轮灯罩(可选) | 1
角度标定台(可选) | 1
主控灯罩 | 1
角 | 8

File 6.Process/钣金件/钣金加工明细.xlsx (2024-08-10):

名称 | 数量 | 备注
外框001 | 6 | 2MM 玻纤
外框002.2.2004 | 3 | 2MM 玻纤
外框003.3.2004 | 3 | 2MM 玻纤
飞轮-2004 | 3 | 嘉立创钣金加工，备注工艺选喷砂，120目

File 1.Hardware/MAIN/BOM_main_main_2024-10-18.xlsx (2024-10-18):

No. | Quantity | Comment | Designator | Footprint | Value | Manufacturer Part | Manufacturer | Supplier Part | Supplier
1 | 21 | 22uF | C1,C2,C3,C4,C5,C6,C13,C14,C15,C16,C17,C18,C25,C26,C27,C28,C29,C30,C38,C42,C43 | C0805 | 22uF | CL21A226MAQNNNE | SAMSUNG(三星) | C45783 | LCSC
2 | 28 | 100nF | C10,C22,C34,C45,C46,C47,C53,C54,C58,C65,C66,C67,C68,C69,C70,C71,C72,C73,C74,C75,C82,C83,C84,C85,C86,C87,C88,C89 | C0402 | 100nF | CL05B104KB54PNC | SAMSUNG(三星) | C307331 | LCSC
3 | 16 | 100nF | C11,C12,C23,C24,C35,C36,C37,C39,C49,C56,C57,C60,C61,C76,C77,C90 | C0402 | 100nF | GRM155R71H104KE14D | muRata(村田) | C77020 | LCSC
4 | 1 | 75pF | C40 | C0402 | 75pF | CC0402GRNPO9BN750 | YAGEO(国巨) | C541421 | LCSC
5 | 2 | 10uF | C41,C44 | C0603 | 10uF | CL10A106KP8NNNC | SAMSUNG(三星) | C19702 | LCSC
6 | 2 | 10uF | C48,C55 | C0402 | 10uF | CL05A106MQ5NUNC | SAMSUNG(三星) | C15525 | LCSC
7 | 2 | 1uF | C51,C59 | C0402 | 1uF | CL05A105KA5NQNC | SAMSUNG(三星) | C52923 | LCSC
8 | 2 | 1.2pF | C63,C64 | C0402 | 1.2pF | GJM1555C1H1R2JB01D | muRata(村田) | C907946 | LCSC
9 | 3 | 10uF | C78,C79,C80 | C0603 | 10uF | CL10A106MA8NRNC | SAMSUNG(三星) | C96446 | LCSC
10 | 1 | 100nF | C81 | C0402 | 100nF | CL05B104KB54PNC | SAMSUNG(三星) |  | LCSC
11 | 1 | XT30PW-M | CN1 | CONN-TH_XT30PW-M |  | XT30PW-M | AMASS(艾迈斯) | C431092 | LCSC
12 | 3 | HC-1.0-6PWT | CN5,CN9,CN10 | CONN-SMD_HCTL_HC-1.0-6PWT |  | HC-1.0-6PWT | HCTL(华灿天禄) | C2845365 | LCSC
13 | 3 | HC-PH-3ALT | CN6,CN7,CN8 | CONN-SMD_3P-P2.00_HCTL_HC-PH-3ALT |  | HC-PH-3ALT | HCTL(华灿天禄) | C2845452 | LCSC
14 | 1 | HC-1.0-4PWT | CN11 | CONN-SMD_4P-P1.00_HCTL_HC-1.0-4PWT |  | HC-1.0-4PWT | HCTL(华灿天禄) | C2845363 | LCSC
15 | 3 | HC-1.0-7PLT | CN12,CN13,CN14 | CONN-SMD_7P-P1.00_HC-1.0-7PLT |  | HC-1.0-7PLT | HCTL(华灿天禄) | C2845375 | LCSC
16 | 9 | 1N5819WS | D1,D2,D3,D4,D5,D6,D7,D8,D9 | SOD-323_L1.8-W1.3-LS2.5-RD |  | 1N5819WS | Hottech(合科泰) | C191023 | LCSC
17 | 2 | BZT52C12S | D10,D11 | SOD-323_L1.8-W1.3-LS2.5-RD |  | BZT52C12S | BORN(伯恩半导体) | C271264 | LCSC
18 | 2 | ESD5Z3.3C | D12,D13 | SOD-523_L1.2-W0.8-LS1.6-BI |  | ESD5Z3.3C | MDD | C502551 | LCSC
19 | 1 | SMAJ12CA | D32 | SMA_L4.2-W2.7-LS5.0-BI |  | SMAJ12CA | GOODWORK(固得沃克) | C908818 | LCSC
20 | 1 | S6125-F-20.0A | F1 | FUSE-SMD_L6.1-W2.6 |  | S6125-F-20.0A | SART(萨特) | C553949 | LCSC
21 | 1 | 10uH | L1 | IND-SMD_L6.0-W6.0_FNR60XXS | 10uH | FNR6045S100MT | cjiang(长江微电) | C168076 | LCSC
22 | 1 | 1.5nH | L3 | R0402 | 1.5nH | VHF100505HQ1N5ST | FH(风华) | C395055 | LCSC
23 | 1 | BLM15AG121SN1D | L4 | L0402 |  | BLM15AG121SN1D | muRata(村田) | C85812 | LCSC
24 | 1 | AN2051-245 | L5 | ANT2051 |  | AN2051-245 | rainsun(霖昱微) | C99727 | LCSC
25 | 18 | WSD3066DN33 | Q1,Q2,Q3,Q4,Q5,Q6,Q7,Q8,Q9,Q10,Q11,Q12,Q13,Q14,Q15,Q16,Q17,Q18 | DFN-8_L3.3-W3.3-P0.65-BL |  | WSD3066DN33 | WINSOK(微硕) | C148386 | LCSC
26 | 1 | AMS1117-3.3V | Q19 | SOT-89-3_L4.5-W2.5-P1.50-LS4.2-BR |  | AMS1117-3.3V | MSKSEMI(美森科) | C5120796 | LCSC
27 | 2 | AP30H50Q | Q20,Q21 | DFN-8_L3.2-W3.1-P0.65-LS3.4-BL |  | AP30H50Q | ALLPOWER(铨力) | C2849568 | LCSC
28 | 1 | CMSC7423B | Q22 | DFN-8_L3.3-W3.3-P0.65-BL_WSD3070DN |  | CMSC7423B | Cmos(广东场效应半导体) | C5203777 | LCSC
29 | 1 | PMBT3904,215 | Q23 | SOT-23_L2.9-W1.3-P1.90-LS2.4-BR |  | PMBT3904,215 | Nexperia(安世) | C8667 | LCSC
30 | 6 | 1kΩ | R1,R9,R11,R19,R21,R29 | R0402 | 1kΩ | RMC04021K1%N | Tyohm(幸亚电阻) | C269675 | LCSC
31 | 6 | 2kΩ | R2,R10,R12,R20,R22,R30 | R0402 | 2kΩ | RMC04022K1%N | Tyohm(幸亚电阻) | C325372 | LCSC
32 | 18 | 10Ω | R3,R4,R5,R6,R7,R8,R13,R14,R15,R16,R17,R18,R23,R24,R25,R26,R27,R28 | R0402 | 10Ω | 0402WGF100JTCE | UNI-ROYAL(厚声) | C25077 | LCSC
33 | 6 | 10kΩ | R31,R32,R33,R68,R69,R70 | R0402 | 10kΩ | RMC040210KFN | Tyohm(幸亚电阻) | C269674 | LCSC
34 | 1 | 100kΩ | R34 | R0402 | 100kΩ | RMC 0402 100K F N | Tyohm(幸亚电阻) | C269673 | LCSC
35 | 1 | 13.3kΩ | R35 | R0402 | 13.3kΩ | RC0402FR-0713K3L | YAGEO(国巨) | C274352 | LCSC
36 | 1 | 0Ω | R36 | R0805 | 0Ω | 0805W8F0000T5E | UNI-ROYAL(厚声) | C17477 | LCSC
37 | 3 | 0Ω | R37,R38,R47 | R0402 | 0Ω | RMC 0402 0R N | Tyohm(幸亚电阻) | C325377 | LCSC
38 | 2 | 120Ω | R39,R40 | R0402 | 120Ω | 0402WGF1200TCE | UNI-ROYAL(厚声) | C25079 | LCSC
39 | 2 | 10kΩ | R41,R44 | R0402 | 10kΩ | 0402WGF1002TCE | UNI-ROYAL(厚声) | C25744 | LCSC
40 | 1 | 510Ω | R42 | R0402 | 510Ω | RMC04025101%N | Tyohm(幸亚电阻) | C325389 | LCSC
41 | 1 | 42.2kΩ | R43 | R0402 | 42.2kΩ | RC0402FR-0742K2L | YAGEO(国巨) | C276270 | LCSC
42 | 21 | 10kΩ | R45,R48,R49,R50,R51,R52,R53,R54,R55,R56,R57,R58,R59,R60,R61,R62,R63,R64,R65,R66,R67 | R0402 | 10kΩ | RC0402FR-0710KL | YAGEO(国巨) | C60490 | LCSC
43 | 1 | 1kΩ | R71 | R0402 | 1kΩ | 0402WGF1001TCE | UNI-ROYAL(厚声) | C11702 | LCSC
44 | 1 | MST-22D18G2 3J | SW1 | SW-SMD_SHOUHAN_MST-22D18G23J_C2875122 |  | MST-22D18G2 3J | SHOU HAN(首韩) | C2875122 | LCSC
45 | 1 | TS-1088-AR02016 | SW2 | SW-SMD_L3.9-W3.0-P4.45 |  | TS-1088-AR02016 | XUNPU(讯普) | C720477 | LCSC
46 | 2 | TS3643TP | SW3,SW4 | KEY-SMD_L6.0-W3.5-LS8.4 |  | TS3643TP | SHOU HAN(首韩) | C398054 | LCSC
47 | 3 | EG2133 | U1,U4,U7 | TSSOP-20_L6.5-W4.4-P0.65-LS6.4-BL |  | EG2133 | EG(屹晶微) | C190343 | LCSC
48 | 6 | CC6920SO-10A | U2,U3,U5,U6,U8,U9 | SOP-8_L5.0-W4.0-P1.27-LS6.2-BL |  | CC6920SO-10A | CrossChip(成都芯进) | C2760488 | LCSC
49 | 1 | TPS54302DDCR | U12 | SOT-23-6_L2.9-W1.6-P0.95-LS2.8-BL |  | TPS54302DDCR | TI(德州仪器) | C311983 | LCSC
50 | 2 | SIT1050QT | U13,U14 | SOP-8_L4.9-W3.9-P1.27-LS6.0-BL |  | SIT1050QT | SIT(芯力特) | C2802043 | LCSC
51 | 2 | - | U15,U17 | QFN-48_L7.0-W7.0-P0.50-BL-EP5.4 | - | ESP32-PICO-D4 | ESPRESSIF 乐鑫 | C193707 | LCSC
52 | 12 | XL-1010RGBC-WS2812B | U16,U19,U20,U21,U22,U23,U24,U25,U26,U27,U28,U29 | LED-SMD_4P-L1.0-W1.0-TL_XL-1010RGBC-WS2812B |  | XL-1010RGBC-WS2812B | XINGLIGHT(成兴光) | C5349953 | LCSC
53 | 1 | BZX584C9V1 | U30 | SOD-523_L1.2-W0.8-LS1.6-FD |  | BZX584C9V1 | CJ(江苏长电/长晶) | C2910113 | LCSC

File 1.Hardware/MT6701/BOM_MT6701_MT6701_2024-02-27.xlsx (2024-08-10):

No. | Quantity | Comment | Designator | Footprint | Value | Manufacturer Part | Manufacturer | Supplier Part | Supplier
1 | 1 | 100nF | C3 | C0402 | 100nF | CL05B104KB54PNC | SAMSUNG(三星) | C307331 | LCSC
2 | 1 | HC-1.25-3PWT | CN3 | CONN-SMD_HC-1.25-3PWT |  | HC-1.25-3PWT | HCTL(华灿天禄) | C2845380 | LCSC
3 | 1 | HC-1.0-7PLT | CN6 | CONN-SMD_7P-P1.00_HC-1.0-7PLT |  | HC-1.0-7PLT | HCTL(华灿天禄) | C2845375 | LCSC
4 | 1 | HC-1.0-3PLT | CN7 | CONN-SMD_3P-P1.00_HC-1.0-3PLT |  | HC-1.0-3PLT | HCTL(华灿天禄) | C2845371 | LCSC
5 | 1 | PZ127V-11-06-H25 | H1 | HDR-TH_6P-P1.27-V-M |  | PZ127V-11-06-H25 | XFCN(兴飞) | C2832273 | LCSC
6 | 1 | MT6701CT-STD | U3 | SOP-8_L4.9-W3.9-P1.27-LS6.0-BL |  | MT6701CT-STD | MagnTek(麦歌恩) | C2856764 | LCSC

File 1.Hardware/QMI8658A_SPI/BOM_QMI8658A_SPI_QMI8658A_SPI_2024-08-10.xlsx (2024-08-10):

No. | Quantity | Comment | Designator | Footprint | Value | Manufacturer Part | Manufacturer | Supplier Part | Supplier
1 | 2 | 100nF | C1,C2 | C0402 | 100nF | CC0402KRX7R7BB104 | YAGEO(国巨) | C60474 | LCSC
2 | 1 | HC-1.0-6PWT | CN2 | CONN-SMD_HCTL_HC-1.0-6PWT |  | HC-1.0-6PWT | HCTL(华灿天禄) | C2845365 | LCSC
3 | 1 | DZ127R-11-06-25 | H1 | HDR-TH_6P-P1.27-V-M-A |  | DZ127R-11-06-25 | DEALON(德艺隆) | C2935946 | LCSC
4 | 1 | 0Ω | R3 | R0402 | 0Ω | 0402WGF0000TCE | UNI-ROYAL(厚声) | C17168 | LCSC
5 | 1 | QMI8658A | U1 | LGA-14_L3.0-W2.5-P0.50-TL |  | QMI8658A | QST(上海矽睿) | C3021082 | LCSC

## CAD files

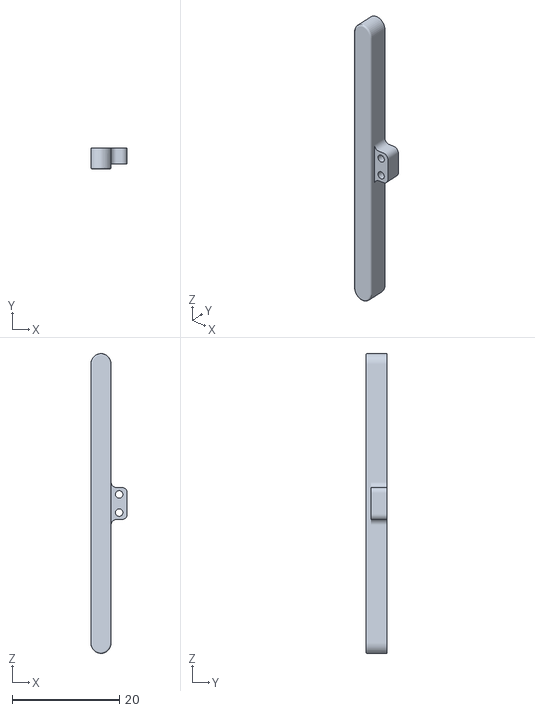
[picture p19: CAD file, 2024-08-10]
6.Process/3D打印/主控灯罩.STL
6.80 x 4.00 x 56.0

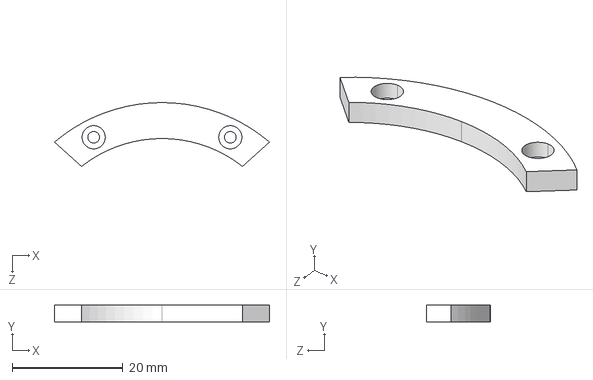
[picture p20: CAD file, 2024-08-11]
6.Process/刹车片/刹车片.STEP
38.9 x 3.00 x 11.5 mm

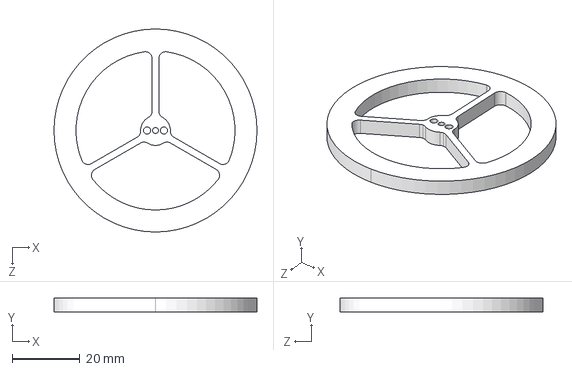
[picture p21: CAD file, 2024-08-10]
6.Process/钣金件/飞轮-2004.STEP
60.0 x 4.00 x 60.0 mm

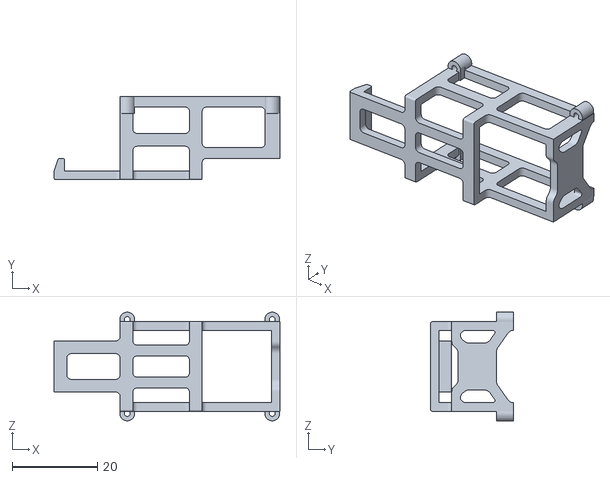
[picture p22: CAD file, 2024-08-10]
6.Process/3D打印/电池安装座002.STL
53.0 x 19.5 x 25.5

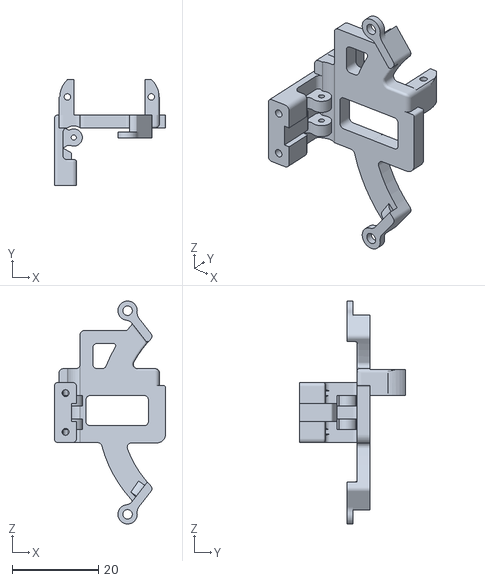
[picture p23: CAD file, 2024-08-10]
6.Process/3D打印/舵机安装座.STL
25.8 x 24.6 x 51.9

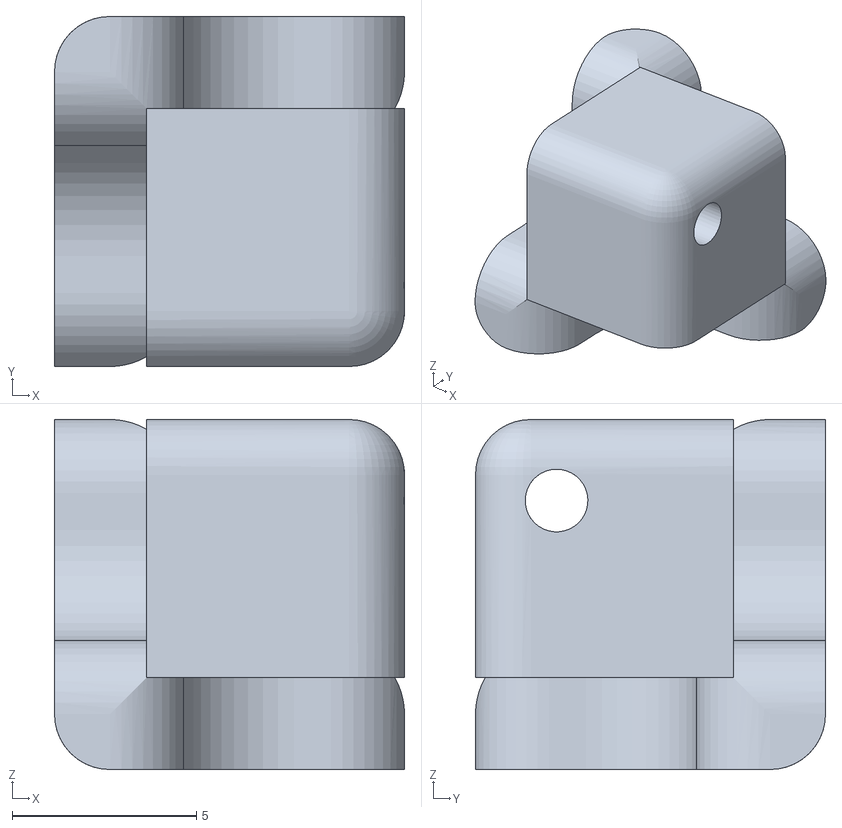
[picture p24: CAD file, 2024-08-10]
6.Process/3D打印/角.STL
9.50 x 9.50 x 9.50

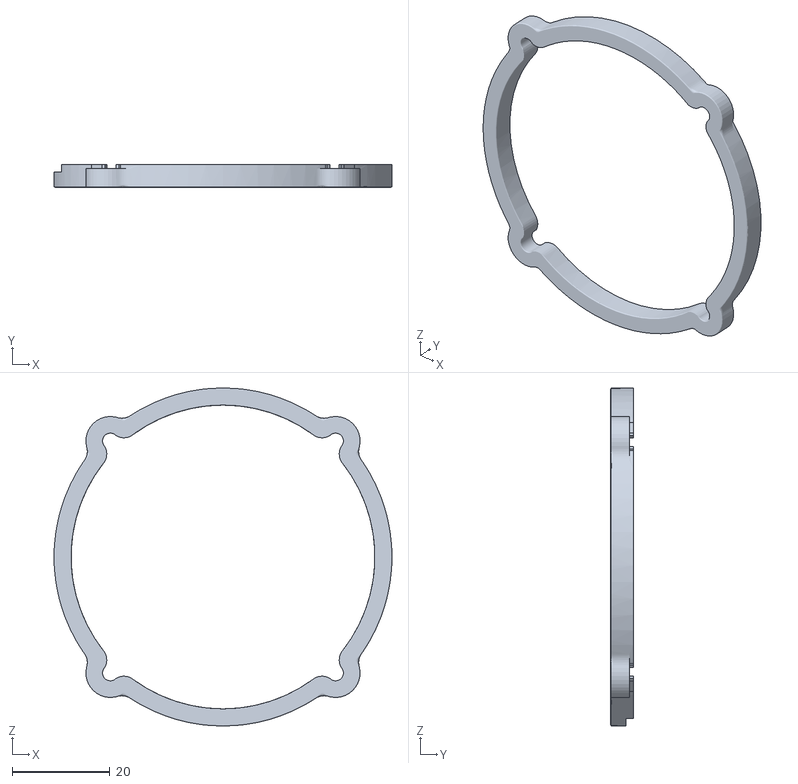
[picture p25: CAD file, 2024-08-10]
6.Process/3D打印/飞轮灯罩(可选).STL
69.0 x 4.60 x 69.0

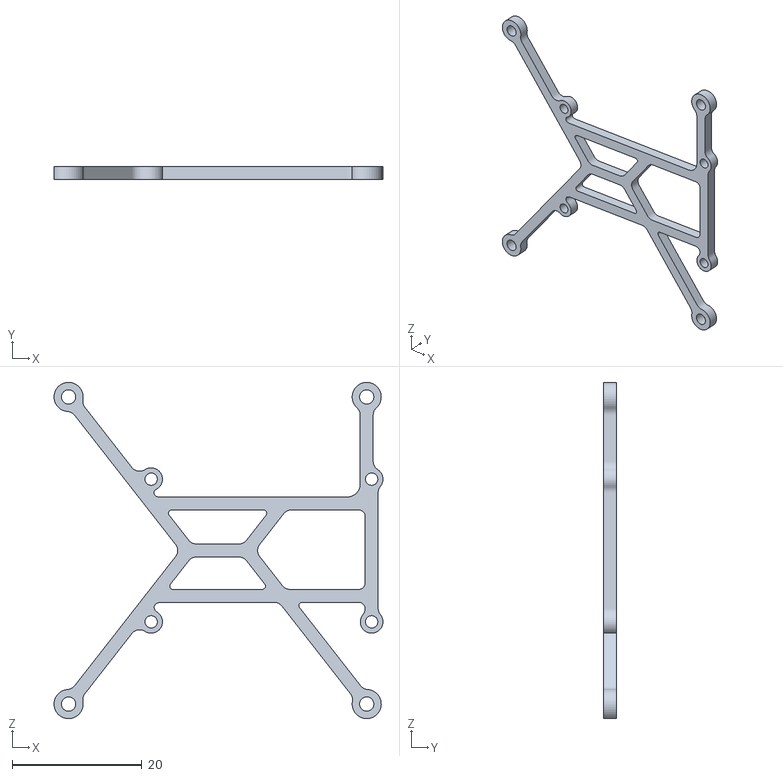
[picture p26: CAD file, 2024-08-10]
6.Process/3D打印/电池安装座001.STL
50.7 x 2.00 x 51.9

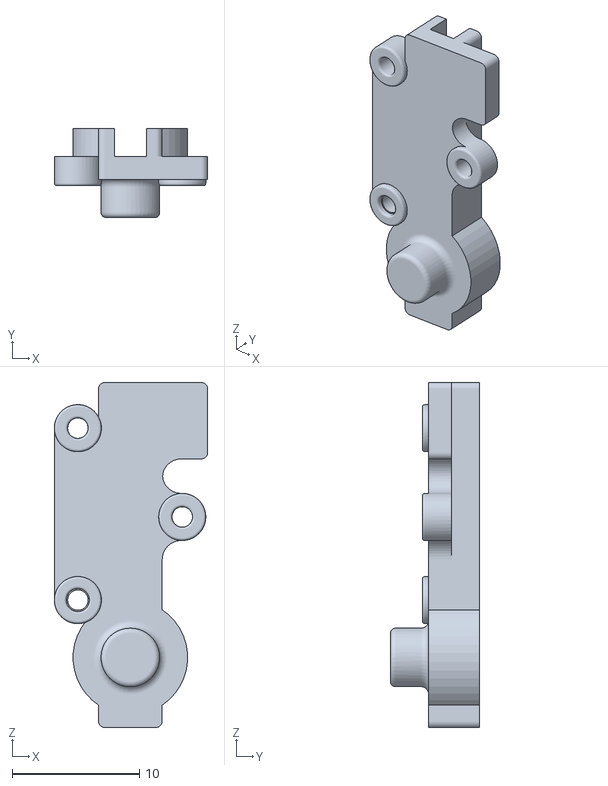
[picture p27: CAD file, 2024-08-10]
6.Process/3D打印/IMU底座-平面.STL
12.0 x 7.00 x 27.1

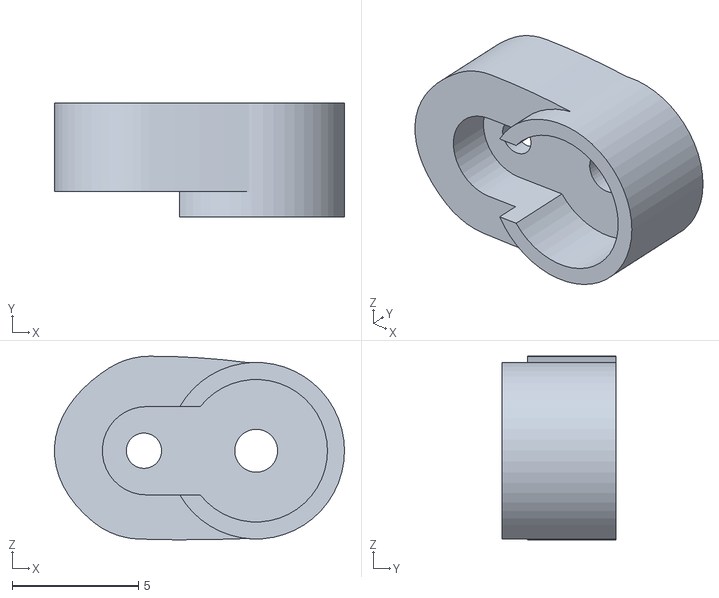
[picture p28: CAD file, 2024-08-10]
6.Process/3D打印/舵机-舵臂-加强.STL
11.5 x 4.50 x 7.28

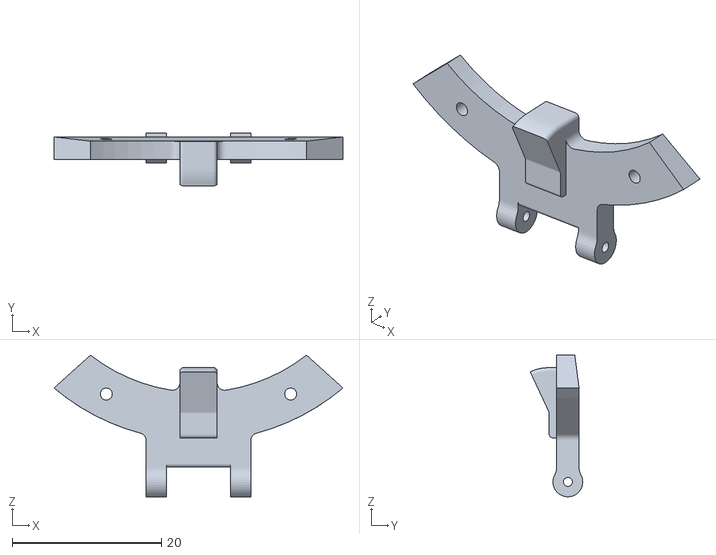
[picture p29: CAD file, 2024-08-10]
6.Process/3D打印/刹车片安装座.STL
38.7 x 7.05 x 19.0

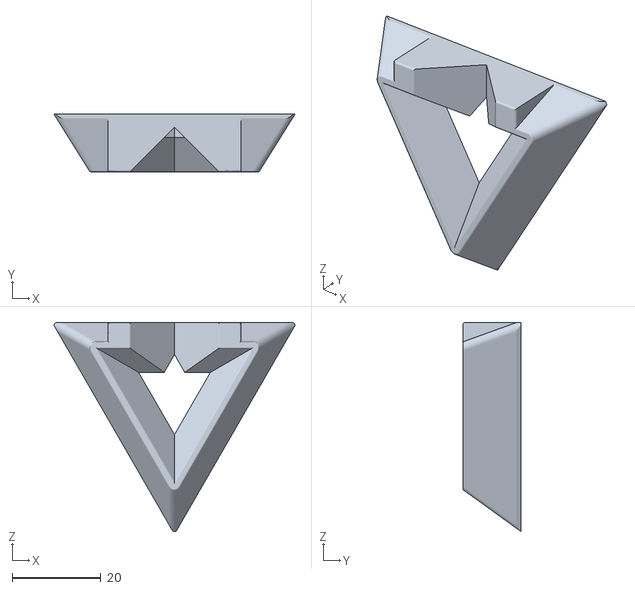
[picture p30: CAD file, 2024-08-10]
6.Process/3D打印/角度标定台(可选).STL
54.2 x 13.0 x 47.0

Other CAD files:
6.Process/钣金件/外框002.2.2004.DWG
6.Process/钣金件/外框003.3.2004.DWG
6.Process/钣金件/外框001.DWG
6.Process/刹车片/刹车片.DWG

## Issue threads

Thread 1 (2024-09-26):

Schematic for the control board

nikhilkalige, 2024-09-26:
Hey, Both of your projects are pretty cool. Would you mind sharing the schematic for the control board pls.

Thank you.

ZhaJiHu, 2024-10-18:
I'm very sorry, I missed it before, but it has now been pushed

Closed 2024-10-18.

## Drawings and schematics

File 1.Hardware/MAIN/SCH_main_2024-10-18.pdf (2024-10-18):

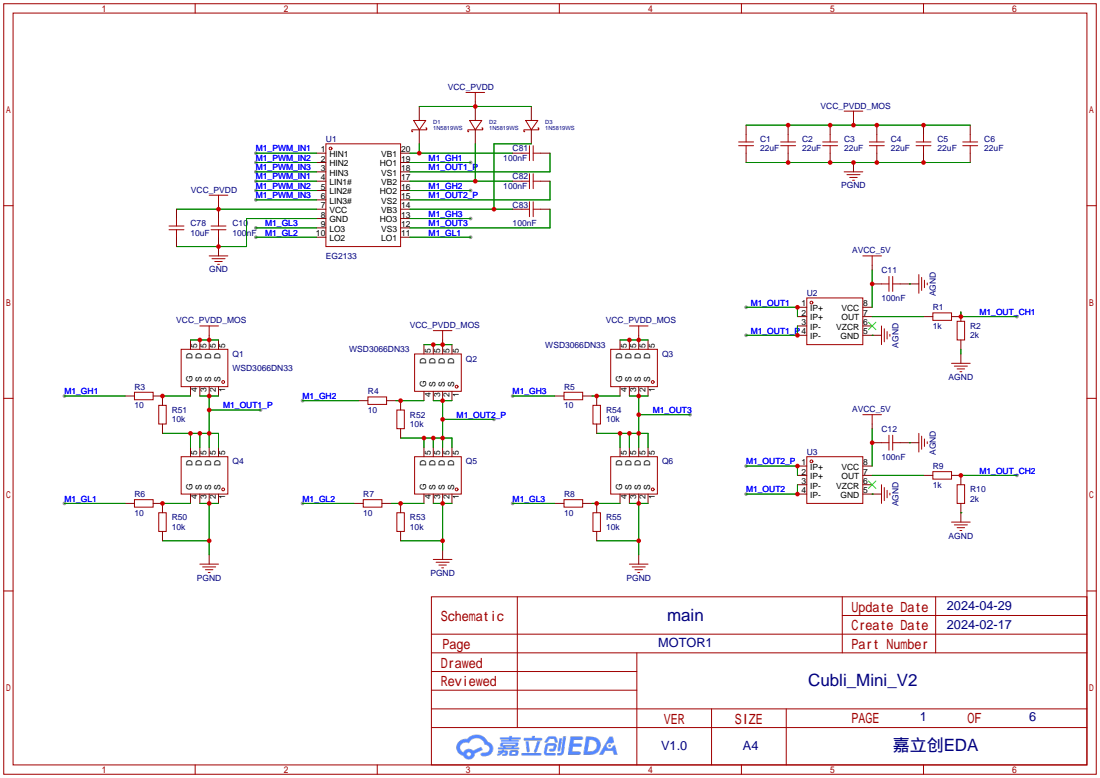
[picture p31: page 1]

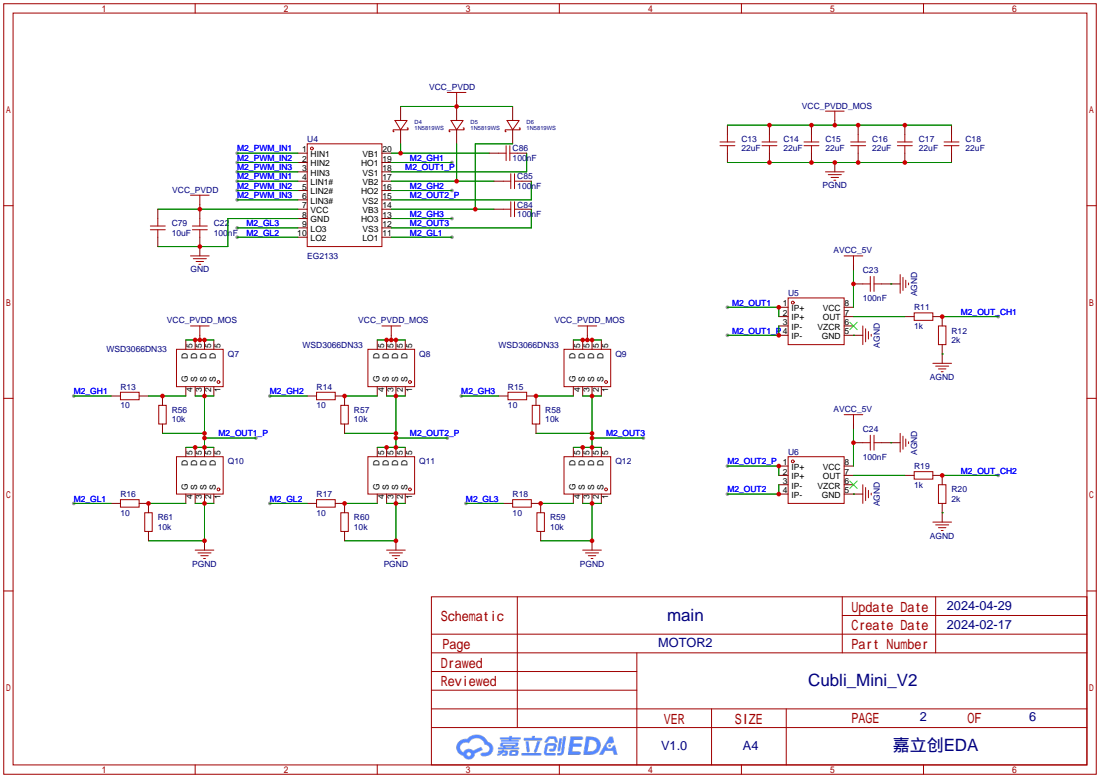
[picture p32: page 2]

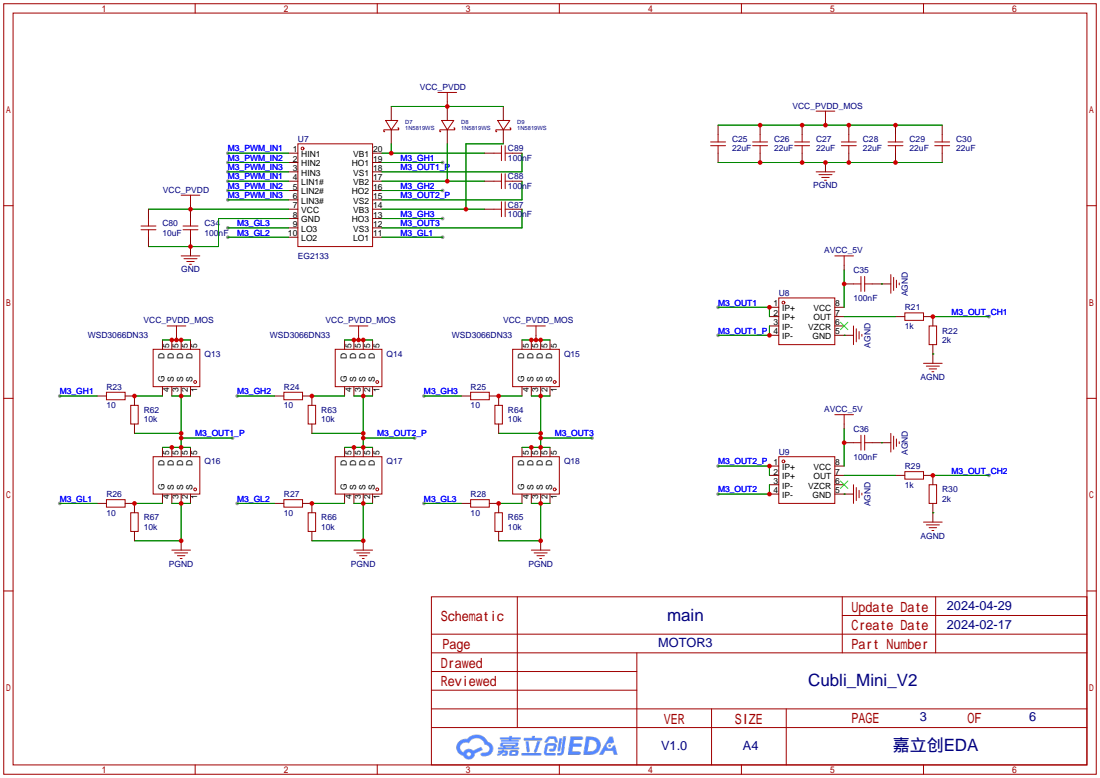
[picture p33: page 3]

# BAT

## 电源开关 电源防反接

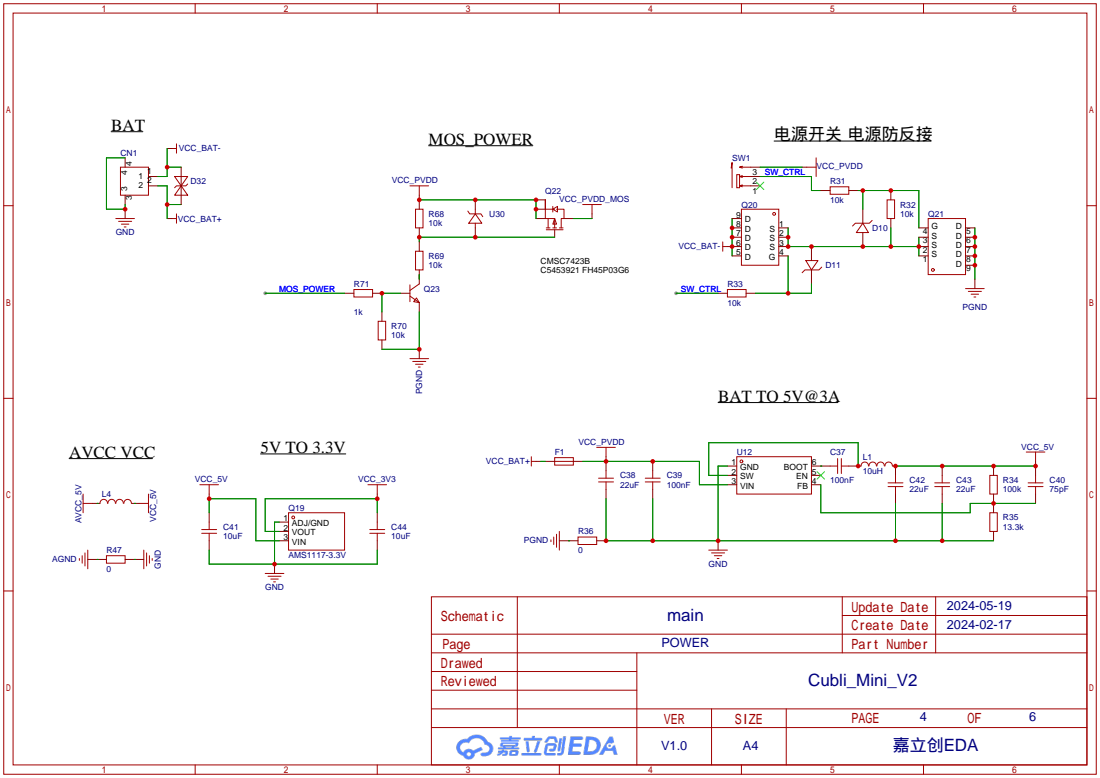
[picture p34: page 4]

# MCU1 CAN1

# MCU2 CAN2

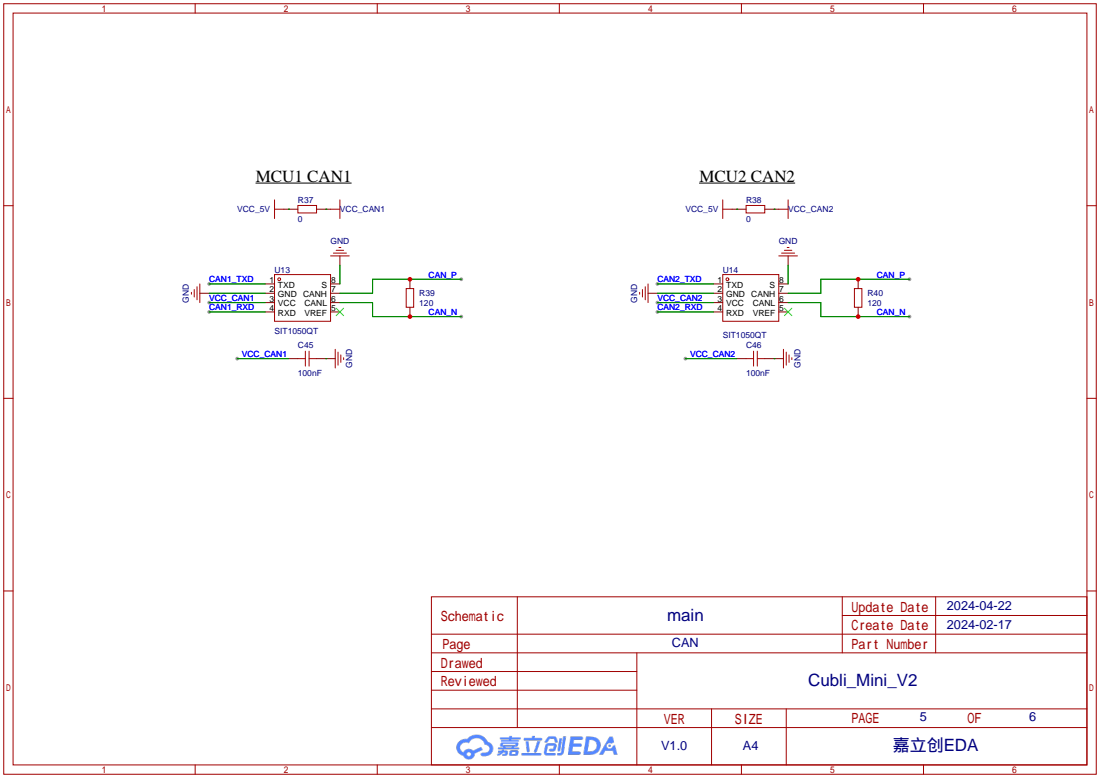
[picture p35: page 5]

MCU1 | MCU1 Download

# MOTOR_CONNECT

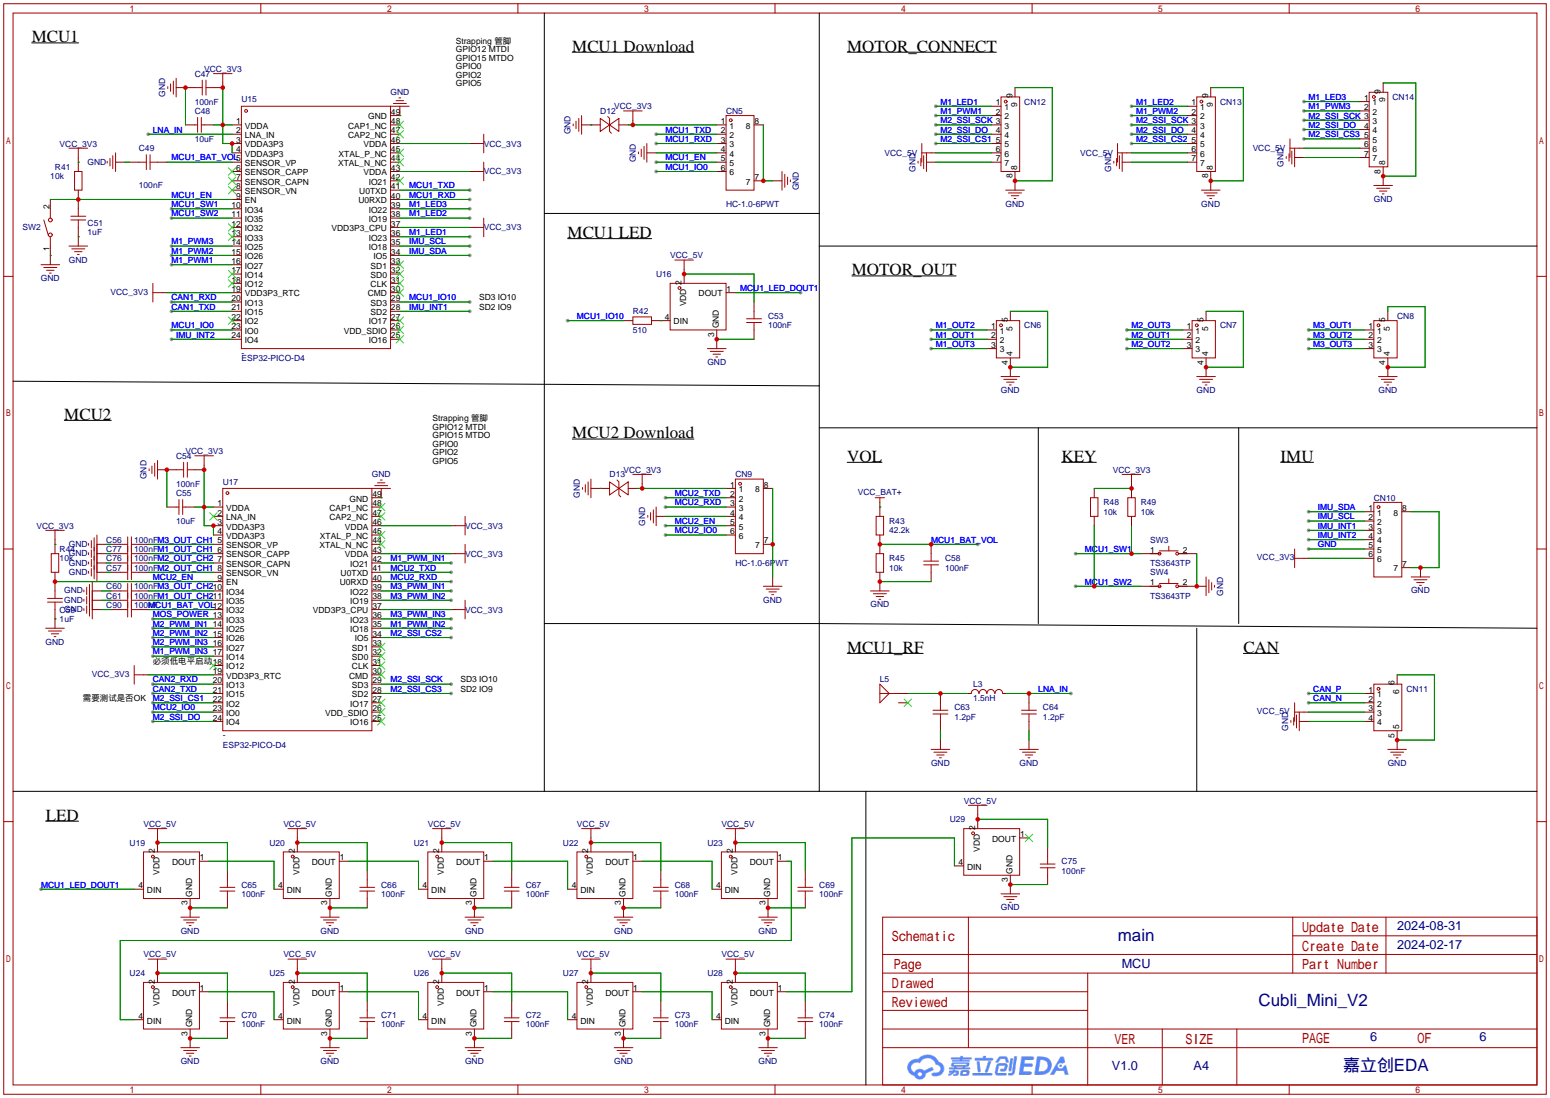
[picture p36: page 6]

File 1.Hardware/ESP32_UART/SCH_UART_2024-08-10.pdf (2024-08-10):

# TYPE_C POWER_5V_TO_3V3

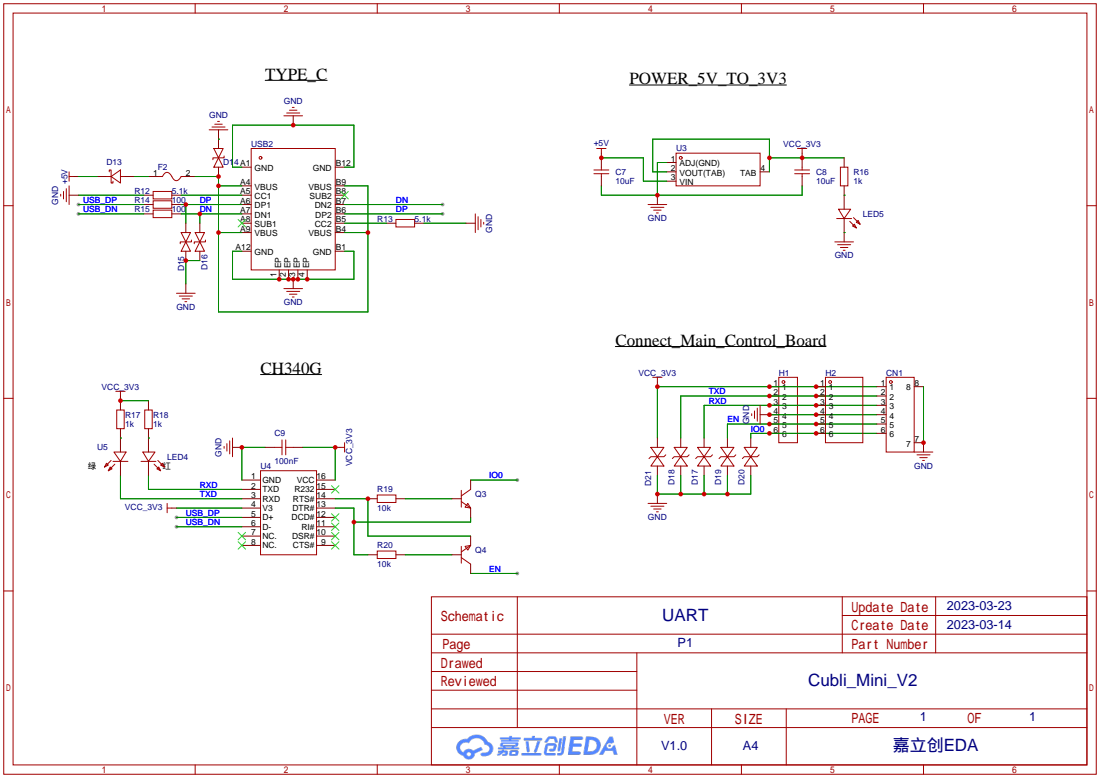
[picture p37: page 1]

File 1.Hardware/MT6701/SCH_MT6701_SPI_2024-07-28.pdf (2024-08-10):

# MOTOR

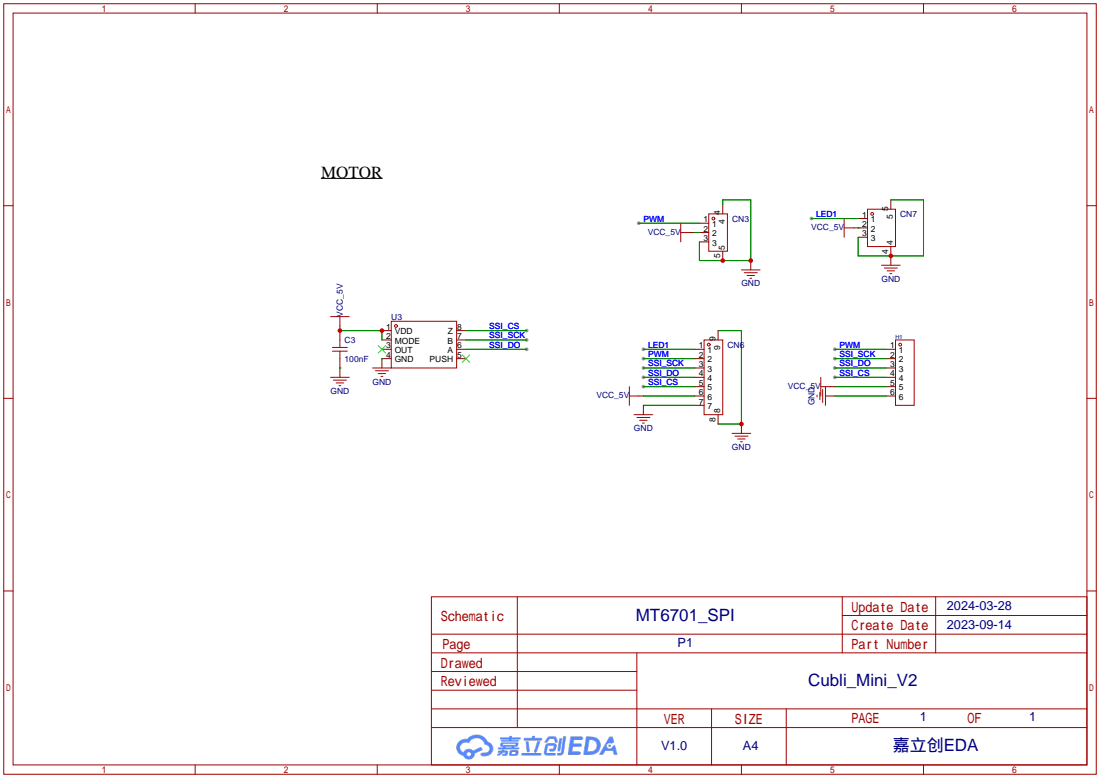
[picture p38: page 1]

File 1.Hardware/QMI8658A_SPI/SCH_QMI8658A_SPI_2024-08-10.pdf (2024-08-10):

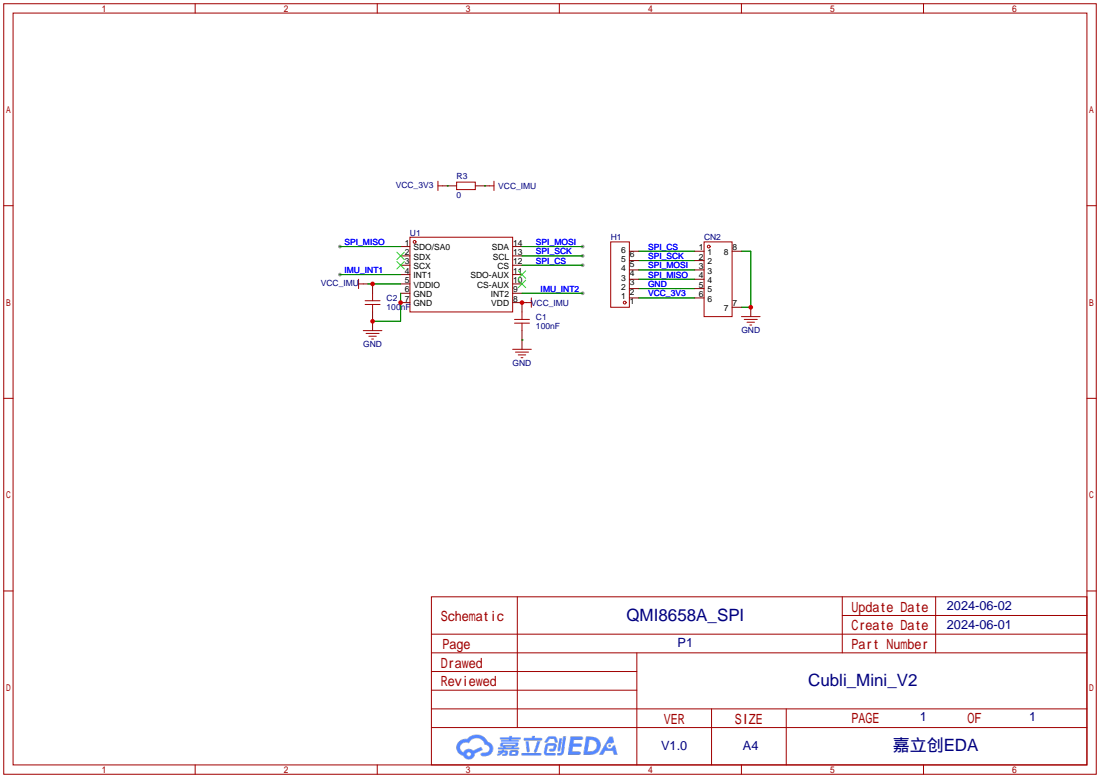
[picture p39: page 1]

CS-AUX 10 SDO-AUX 11 CS 12 SCL 13 SDA 14

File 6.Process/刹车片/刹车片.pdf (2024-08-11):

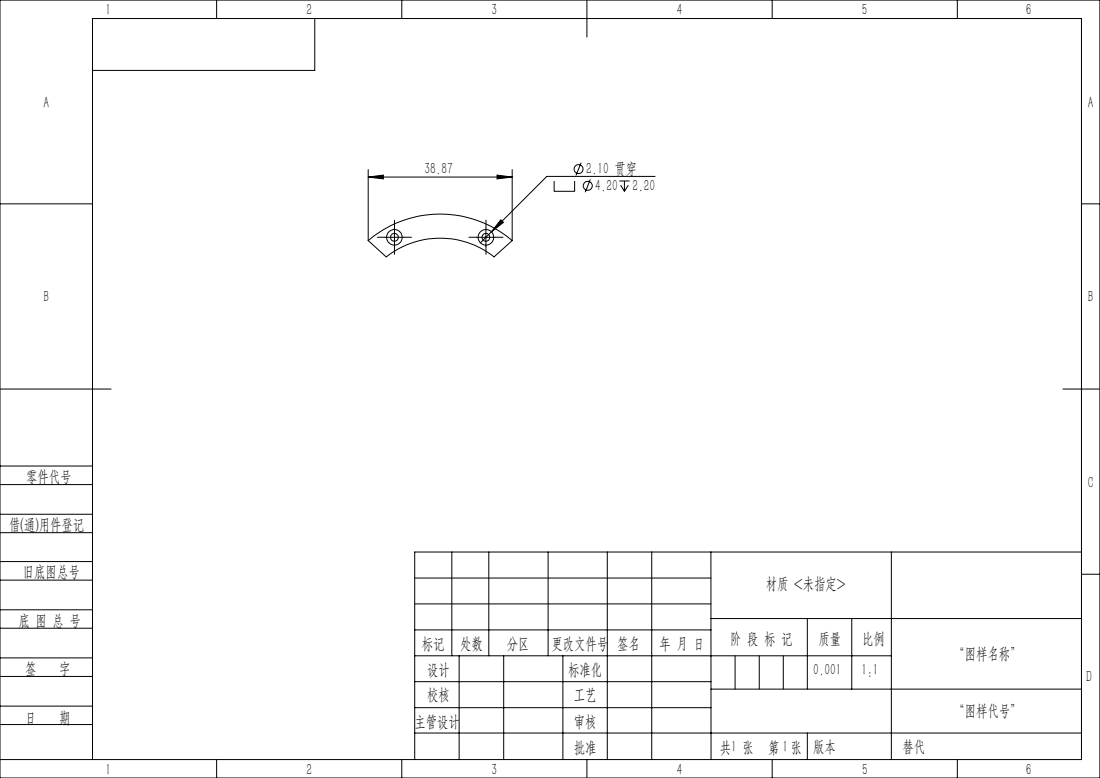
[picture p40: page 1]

材质 <未指定>

阶 段 标 记 | 质量 | 比例 | “图样名称”

标记 | 处数 | 分区 | 更改文件号 | 签名 | 年 月 日

“图样代号”

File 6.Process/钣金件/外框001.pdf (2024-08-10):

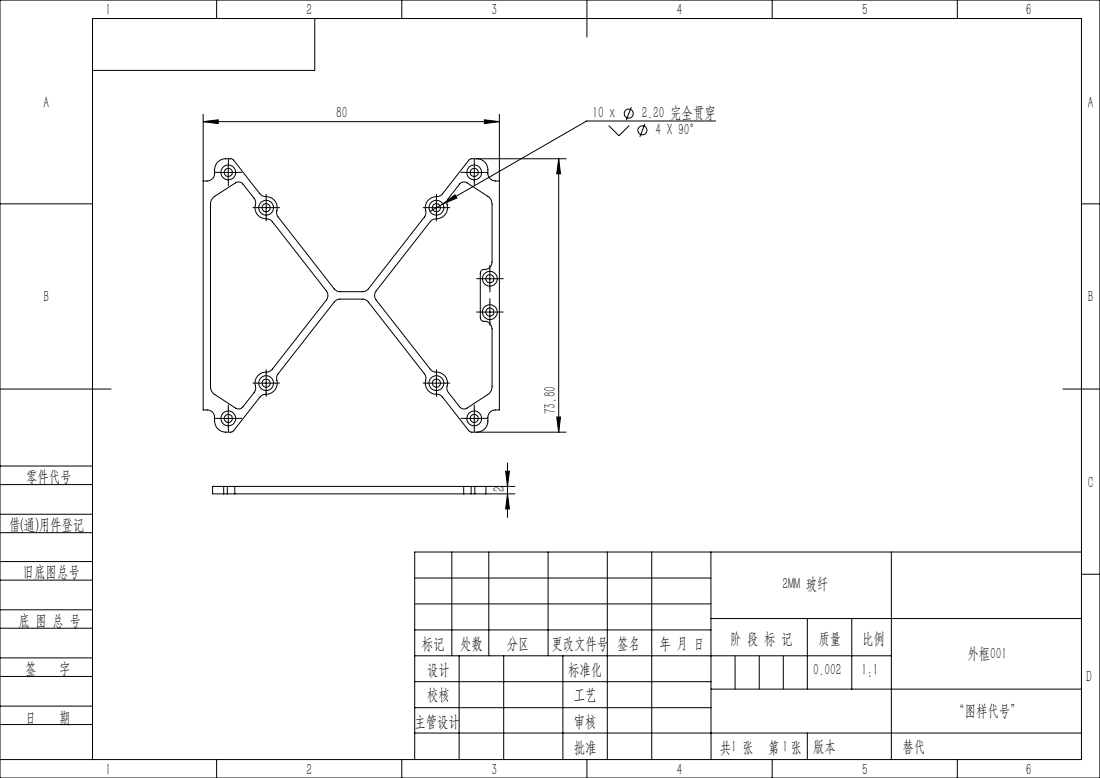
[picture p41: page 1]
2.20 完全贯穿

标记 | 处数 | 分区 | 更改文件号 | 签名 | 年 月 日

“图样代号”

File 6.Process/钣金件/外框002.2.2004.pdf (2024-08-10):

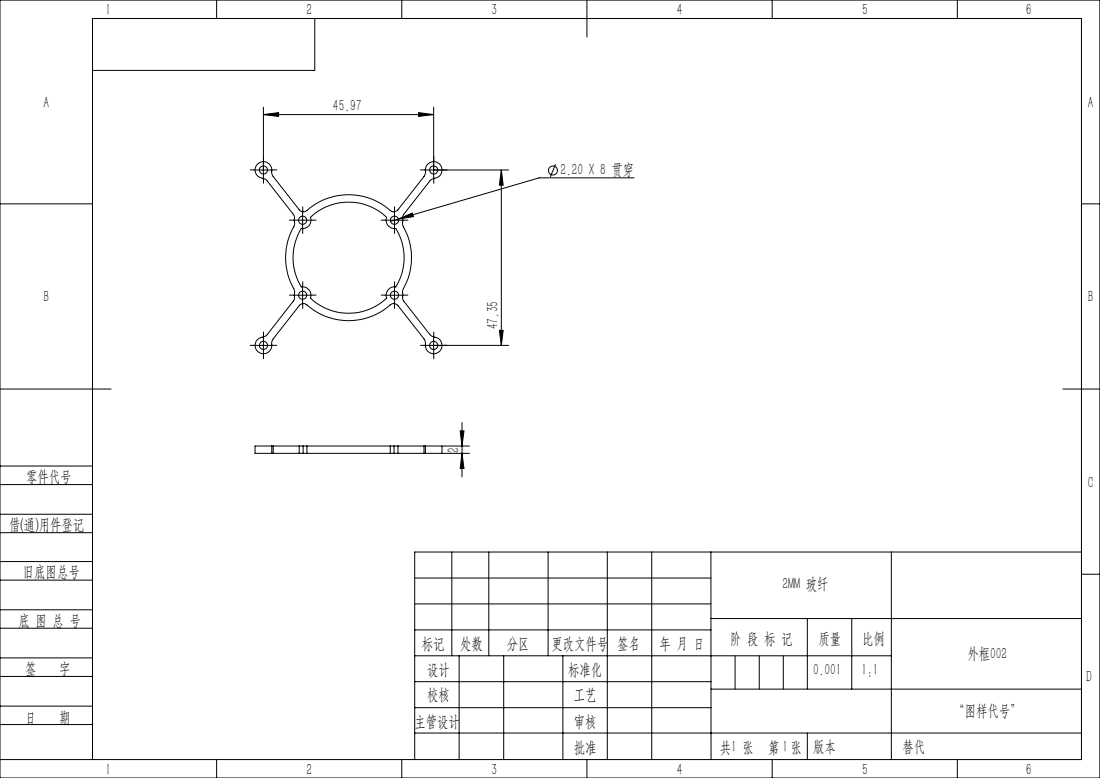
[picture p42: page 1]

标记 | 处数 | 分区 | 更改文件号 | 签名 | 年 月 日

“图样代号”

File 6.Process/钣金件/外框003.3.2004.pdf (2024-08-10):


标记 | 处数 | 分区 | 更改文件号 | 签名 | 年 月 日

“图样代号”

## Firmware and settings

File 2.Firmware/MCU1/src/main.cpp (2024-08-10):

#include <Adafruit_NeoPixel.h>
#include <Arduino.h>

#include "bsp/battery.h"
#include "bsp/can.h"
#include "bsp/key.h"
#include "bsp/servo_motor.h"
#include "comm/comm.h"
#include "comm/time.h"
#include "config/config.h"
#include "control/angle_offset_calibration.h"
#include "control/p_balance_control.h"
#include "control/param.h"
#include "control/pid.h"
#include "control/serial_commander.h"
#include "control/u_balance_control.h"
#include "control/wifi_commander.h"
#include "imu/ahrs.h"
#include "imu/qmi8658_driver.h"

using namespace CubliMini::Bsp;
using namespace CubliMini::Comm;
using namespace CubliMini::Control;

Adafruit_NeoPixel system_strip =
    Adafruit_NeoPixel(SYSTEM_LED_NUM, SYSTEM_LED_PIN, NEO_GRB + NEO_KHZ800);
Adafruit_NeoPixel motor1_strip =
    Adafruit_NeoPixel(MOTOR_LED_NUM, MOTOR1_LED_PIN, NEO_GRB + NEO_KHZ800);
Adafruit_NeoPixel motor2_strip =
    Adafruit_NeoPixel(MOTOR_LED_NUM, MOTOR2_LED_PIN, NEO_GRB + NEO_KHZ800);
Adafruit_NeoPixel motor3_strip =
    Adafruit_NeoPixel(MOTOR_LED_NUM, MOTOR3_LED_PIN, NEO_GRB + NEO_KHZ800);

ServoMotor servo_motor1(SERVO_MOTOR_1_PIN, 13);
ServoMotor servo_motor2(SERVO_MOTOR_2_PIN, 14);
ServoMotor servo_motor3(SERVO_MOTOR_3_PIN, 15);

// 暂时不使用key
KeyDriver key1;
KeyDriver key2;

void CmdTask(void *parameter);
void ImuTask(void *parameter);
void CanRecTask(void *parameter);
void ControlTask(void *parameter);
void CanSendTask(void *parameter);
void MotorLedTask(void *parameter);

CubliMini::Bsp::CanDriver can_;
CubliMini::ImuDriver::ImuDriverBase *imu_driver_ptr_  = nullptr;
CubliMini::Imu::AHRS *ahrs_ptr                        = nullptr;
CubliMini::Control::WifiCommander *wifi_commander_ptr = nullptr;
Battery battery_;

QueueHandle_t xQueueImu;
QueueHandle_t xQueueCanSend;
QueueHandle_t xQueueCanGet;

float cal_angle_kp = 0.000022f;
UBalanceControl U_balance_control(Param::GetInstance()->GetUAxisParam(), cal_angle_kp);
PBalanceControl p_balance_control(Param::GetInstance()->GetPAxisParam(), cal_angle_kp);

void setup()
{
    Serial.begin(115200);
    system_strip.begin();
    system_strip.setBrightness(50);
    system_strip.setPixelColor(0, system_strip.Color(255, 0, 0));
    system_strip.show();
    servo_motor1.re_init();
    servo_motor2.re_init();
    servo_motor3.re_init();

    imu_driver_ptr_ = new CubliMini::ImuDriver::Qmi8658Driver(&Wire);
    if (imu_driver_ptr_->Init() != 0)
    {
        for(;;)
        {
            Serial.println("Failed to find imu - check your wiring!");
            delay(1000);
        }
    }
    ahrs_ptr = new CubliMini::Imu::AHRS(imu_driver_ptr_, IMU_STATIC_GYRO_THRESHOLD);

    Param::GetInstance()->Load();

    motor1_strip.begin();
    motor1_strip.setBrightness(50);
    motor1_strip.show();

    motor2_strip.begin();
    motor2_strip.setBrightness(50);
    motor2_strip.show();

    motor3_strip.begin();
    motor3_strip.setBrightness(50);
    motor3_strip.show();

    key1.Init(SYSTEM_KEY1_PIN);
    key2.Init(SYSTEM_KEY2_PIN);

    xQueueImu     = xQueueCreate(1, sizeof(ImuData_t));
    xQueueCanSend = xQueueCreate(1, sizeof(PBalanceControl::MotorControl));
    xQueueCanGet  = xQueueCreate(1, sizeof(PBalanceControl::MotorSpeed));
    can_.Init(CAN_TXD_PIN, CAN_RXD_PIN, CAN_SPEED_1000KBPS);

    xTaskCreatePinnedToCore(CmdTask, "cmd task", 30000, NULL, 3, NULL, 1);
    xTaskCreatePinnedToCore(ImuTask, "imu task", 10000, NULL, 6, NULL, 1);
    xTaskCreatePinnedToCore(CanRecTask, "can task", 10000, NULL, 6, NULL, 1);
    xTaskCreatePinnedToCore(CanSendTask, "can1 task", 10000, NULL, 4, NULL, 1);
    xTaskCreatePinnedToCore(ControlTask, "control task", 20000, NULL, 5, NULL, 1);
    xTaskCreatePinnedToCore(MotorLedTask, "MOTOR1 LED task", 10000, NULL, 2, NULL, 1);
    delay(1000);
}

PBalanceControl::MotorSpeed g_get_motor_speed;
void CanRecTask(void *parameter)
{
    for (;;)
    {
        PBalanceControl::MotorSpeed get_motor_speed;
        if (can_.CanGetMotorSpeed(get_motor_speed.ch1, get_motor_speed.ch2, get_motor_speed.ch3))
        {
            g_get_motor_speed = get_motor_speed;
        }
    }
}

void CanSendTask(void *parameter)
{
    for (;;)
    {
        PBalanceControl::MotorControl send_motor_control;
        if (xQueueReceive(xQueueCanSend, &send_motor_control, portMAX_DELAY) == pdTRUE)
        {
            can_.CanSendMotorSpeed(
                send_motor_control.ch1,
                send_motor_control.ch2,
                send_motor_control.ch3,
                send_motor_control.value,
                send_motor_control.control_mode);
        }
    }
}

struct ImuRotationAngle_t
{
    float x;
    float y;
    float z;
};

ImuRotationAngle_t imu_rotation_angle = {0, -40, 0};

void ImuTask(void *parameter)
{
    ConvertAngularVelocity gyro_conv;
    for (;;)
    {
        ahrs_ptr->AhrsLoop();
        gyro_conv.Loop(
            imu_rotation_angle.y,
            ahrs_ptr->imu_data_.gyro.gy,
            ahrs_ptr->imu_data_.gyro.gx,
            ahrs_ptr->imu_data_.gyro.gz,
            ahrs_ptr->imu_data_.gyro.gy,
            ahrs_ptr->imu_data_.gyro.gz);
        ahrs_ptr->imu_data_.gyro.gz = -ahrs_ptr->imu_data_.gyro.gz;
        xQueueSend(xQueueImu, &ahrs_ptr->imu_data_, 0);
    }
}

enum RunMode_e
{
    NORMAL_MODE = 0x00,  // 普通模式
    U_JUMP_MODE,         // 边起跳模式
    U_JUMPING_MODE,      // 起跳中
    U_BALANCE_MODE,      // 边平衡模式
    POINT_JUMP_MODE,     // 点起跳模式
    POINT_JUMPING_MODE,  // 点起跳中
    POINT_BALANCE_MODE   // 点平衡
};

int mode          = NORMAL_MODE;
float yaw_control = 0.0f;  // 控制yaw的自旋
float slot_param  = 1.3;   // 刹车系数

struct MotorjumpValue_t
{
    float set_motor_speed;
    int set_servo_pos;
    int servo_int_pos;
};

struct jumpValue_t
{
    MotorjumpValue_t m1;
    MotorjumpValue_t m2;
    MotorjumpValue_t m3;
};

jumpValue_t jump_value = {
    .m1 {-340, 100, 70},
     .m2 {-340, 100, 56},
     .m3 {-570, 100, 62}
};

void WifiCommanderTask(void *parameter)
{
    for (;;)
    {
        wifi_commander_ptr->WaitClientConnect();
        wifi_commander_ptr->TcpClientUnpack();
    }
}

void CmdTask(void *parameter)
{
    CubliMini::Control::SerialCommander serial_commander;
    wifi_commander_ptr = new CubliMini::Control::WifiCommander();

    REGISTER_COMMAND_FLOAT(serial_commander, "M", mode);
    AxisParam_t &u_param = Param::GetInstance()->GetUAxisParam();
    REGISTER_COMMAND_FLOAT(serial_commander, "SUA", u_param.angle_offset);
    REGISTER_COMMAND_FLOAT(serial_commander, "SUP", u_param.kp);
    REGISTER_COMMAND_FLOAT(serial_commander, "SUV", u_param.kv);
    REGISTER_COMMAND_FLOAT(serial_commander, "SUS", u_param.ks);

    PBalanceControl::PAxisParam &p_param = Param::GetInstance()->GetPAxisParam();
    REGISTER_COMMAND_FLOAT(serial_commander, "SPXA", p_param.x.angle_offset);
    REGISTER_COMMAND_FLOAT(serial_commander, "SPXP", p_param.x.kp);
    REGISTER_COMMAND_FLOAT(serial_commander, "SPXV", p_param.x.kv);
    REGISTER_COMMAND_FLOAT(serial_commander, "SPXS", p_param.x.ks);

    REGISTER_COMMAND_FLOAT(serial_commander, "SPYA", p_param.y.angle_offset);
    REGISTER_COMMAND_FLOAT(serial_commander, "SPYP", p_param.y.kp);
    REGISTER_COMMAND_FLOAT(serial_commander, "SPYV", p_param.y.kv);
    REGISTER_COMMAND_FLOAT(serial_commander, "SPYS", p_param.y.ks);

    REGISTER_COMMAND_FLOAT(serial_commander, "SPZA", p_param.z.angle_offset);
    REGISTER_COMMAND_FLOAT(serial_commander, "SPZP", p_param.z.kp);
    REGISTER_COMMAND_FLOAT(serial_commander, "SPZV", p_param.z.kv);
    REGISTER_COMMAND_FLOAT(serial_commander, "SPZS", p_param.z.ks);

    REGISTER_COMMAND_FLOAT(serial_commander, "M1_JUMP_SPEED", jump_value.m1.set_motor_speed);
    REGISTER_COMMAND_FLOAT(serial_commander, "M2_JUMP_SPEED", jump_value.m2.set_motor_speed);
    REGISTER_COMMAND_FLOAT(serial_commander, "M3_JUMP_SPEED", jump_value.m3.set_motor_speed);

    REGISTER_COMMAND_FLOAT(serial_commander, "IMU_ROTATION_X", imu_rotation_angle.x);
    REGISTER_COMMAND_FLOAT(serial_commander, "IMU_ROTATION_Y", imu_rotation_angle.y);
    REGISTER_COMMAND_FLOAT(serial_commander, "IMU_ROTATION_Z", imu_rotation_angle.z);

    REGISTER_COMMAND_FLOAT(serial_commander, "YAW_CONTROL", yaw_control);
    REGISTER_COMMAND_FLOAT(serial_commander, "slot_param", slot_param);
    REGISTER_COMMAND_FLOAT(serial_commander, "cal_angle_kp", cal_angle_kp);

    serial_commander.Register("SERVO1", [&](const std::string &value) {
        float modeVariable = std::stof(value);
        servo_motor1.setDegree(modeVariable);
        jump_value.m1.servo_int_pos = modeVariable;
        printf("SERVO1 setDegree: %.3f\n", modeVariable);
    });

    serial_commander.Register("SERVO2", [&](const std::string &value) {
        float modeVariable          = std::stof(value);
        jump_value.m2.servo_int_pos = modeVariable;
        servo_motor2.setDegree(modeVariable);
        printf("SERVO2 setDegree: %.3f\n", modeVariable);
    });

    serial_commander.Register("SERVO3", [&](const std::string &value) {
        float modeVariable = std::stof(value);
        servo_motor3.setDegree(modeVariable);
        jump_value.m3.servo_int_pos = modeVariable;
        printf("SERVO3 setDegree: %.3f\n", modeVariable);
    });

    serial_commander.Register("SET_MOTOR1_SPEED", [&](const std::string &value) {
        float modeVariable = std::stof(value);
        printf("MOTOR1 set speed: %d rad/s\n", modeVariable);
    });

    serial_commander.Register("SET_MOTOR2_SPEED", [&](const std::string &value) {
        float modeVariable = std::stof(value);
        printf("MOTOR2 set speed: %d rad/s\n", modeVariable);
    });

    serial_commander.Register("SET_MOTOR3_SPEED", [&](const std::string &value) {
        float modeVariable = std::stof(value);
        printf("MOTOR3 set speed: %d rad/s\n", modeVariable);
    });

    serial_commander.Register("SET_SERVO3_ANGLE", [&](const std::string &value) {
        float modeVariable = std::stof(value);
        printf("SERVO3_ANGLE set angle: %0.3f d\n", modeVariable);
    });

    serial_commander.Register("GU", [](const std::string &value) {
        AxisParam_t &param = Param::GetInstance()->GetUAxisParam();
        printf(
            "GU angle_offset:[%0.3f] kp:[%0.3f] kv:[%0.3f] ks:[%0.3f]\n",
            param.angle_offset,
            param.kp,
            param.kv,
            param.ks);
    });

    serial_commander.Register("GP", [](const std::string &value) {
        PBalanceControl::PAxisParam &param = Param::GetInstance()->GetPAxisParam();
        printf(
            "GP\n x angle_offset:[%0.3f] kp:[%0.3f] kv:[%0.3f] ks:[%0.3f] \n y "
            "angle_offset:[%0.3f] kp:[%0.3f] kv:[%0.3f] ks:[%0.3f] \n z angle_offset:[%0.3f] "
            "kp:[%0.3f] kv:[%0.3f] ks:[%0.3f] \n",
            param.x.angle_offset,
            param.x.kp,
            param.x.kv,
            param.x.ks,
            param.y.angle_offset,
            param.y.kp,
            param.y.kv,
            param.y.ks,
            param.z.angle_offset,
            param.z.kp,
            param.z.kv,
            param.z.ks);
    });

    serial_commander.Register("SAVE_P", [](const std::string &value) {
        PBalanceControl::PAxisParam param = Param::GetInstance()->GetPAxisParam();
        printf(
            "SAVE\nP\n x angle_offset:[%0.3f] kp:[%0.3f] kv:[%0.3f] ks:[%0.3f] \n y "
            "angle_offset:[%0.3f] kp:[%0.3f] kv:[%0.3f] ks:[%0.3f] \n z angle_offset:[%0.3f] "
            "kp:[%0.3f] kv:[%0.3f] ks:[%0.3f] \n",
            param.x.angle_offset,
            param.x.kp,
            param.x.kv,
            param.x.ks,
            param.y.angle_offset,
            param.y.kp,
            param.y.kv,
            param.y.ks,
            param.z.angle_offset,
            param.z.kp,
            param.z.kv,
            param.z.ks);
        Param::GetInstance()->SavePBalanceParam();
    });

    serial_commander.Register("SAVE_U", [](const std::string &value) {
        AxisParam_t u_param = Param::GetInstance()->GetUAxisParam();
        printf(
            "u\n angle_offset:[%0.3f] kp:[%0.3f] kv:[%0.3f] ks:[%0.3f]\n",
            u_param.angle_offset,
            u_param.kp,
            u_param.kv,
            u_param.ks);
        Param::GetInstance()->SaveUBalanceParam();
    });

    serial_commander.Register("RESET", [](const std::string &value) {
        Param::GetInstance()->FirstWriteParamToEeprom();
        Param::GetInstance()->LoadParam();
        PBalanceControl::PAxisParam param = Param::GetInstance()->GetPAxisParam();
        printf(
            "SAVE\nP\n x angle_offset:[%0.3f] kp:[%0.3f] kv:[%0.3f] ks:[%0.3f] \n y "
            "angle_offset:[%0.3f] kp:[%0.3f] kv:[%0.3f] ks:[%0.3f] \n z angle_offset:[%0.3f] "
            "kp:[%0.3f] kv:[%0.3f] ks:[%0.3f] \n",
            param.x.angle_offset,
            param.x.kp,
            param.x.kv,
            param.x.ks,
            param.y.angle_offset,
            param.y.kp,
            param.y.kv,
            param.y.ks,
            param.z.angle_offset,
            param.z.kp,
            param.z.kv,
            param.z.ks);
        AxisParam_t u_param = Param::GetInstance()->GetUAxisParam();
        printf(
            "u\n angle_offset:[%0.3f] kp:[%0.3f] kv:[%0.3f] ks:[%0.3f]\n",
            u_param.angle_offset,
            u_param.kp,
            u_param.kv,
            u_param.ks);
    });

    wifi_commander_ptr->SetCmds(serial_commander.GetCmds());
    wifi_commander_ptr->ConnectWifi();
    if (wifi_commander_ptr->GetConnectStatus() == WifiConnectStatus_e::eWIFI_SUCCESS)
    {
        // core 0
        xTaskCreatePinnedToCore(WifiCommanderTask, "WifiCommanderTask", 30000, NULL, 7, NULL, 0);
    }

    uint32_t count = 0;
    for (;;)
    {
        ++count;
        serial_commander.Run(Serial);
        if (count % 10 == 0)
        {
            float angle_d = ahrs_ptr->imu_data_.angle.pitch -
                            Param::GetInstance()->GetUAxisParam().angle_offset;

            printf(
                "%0.3f %0.3f %0.3f %0.3f %0.3f %0.3f\n",
                ahrs_ptr->imu_data_.angle.pitch,
                ahrs_ptr->imu_data_.angle.roll,
                ahrs_ptr->imu_data_.angle.yaw,
                ahrs_ptr->imu_data_.gyro.gy,
                ahrs_ptr->imu_data_.gyro.gx,
                ahrs_ptr->imu_data_.gyro.gz);
        }
        {
            // 暂不使用
            KeyAction_e key1_action = key1.GetKeyAction();
            KeyAction_e key2_action = key2.GetKeyAction();

            if (key1_action == KeyAction_e::eKEY_ACTION_SHORT_PRESS)
            {
                printf("key1 eKEY_ACTION_SHORT_PRESS\n");
            }

            if (key1_action == KeyAction_e::eKEY_ACTION_LONG_PRESS)
            {
                printf("key1 eKEY_ACTION_LONG_PRESS\n");
            }

            if (key2_action == KeyAction_e::eKEY_ACTION_SHORT_PRESS)
            {
                printf("key2 eKEY_ACTION_SHORT_PRESS\n");
            }

            if (key2_action == KeyAction_e::eKEY_ACTION_LONG_PRESS)
            {
                printf("key2 eKEY_ACTION_LONG_PRESS\n");
            }
        }
        delay(10);
    }
}
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
void loop()
{
    rainbow(20);
    rainbowCycle(20);
}

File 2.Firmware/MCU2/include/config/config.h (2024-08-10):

#pragma once
#include <Arduino.h>

#define MOTOR_PP 7
#define MOTOR_PHASE_RESISTANCE 0.208f
#define MOTOR_KV 1800

#define MOTOR1_CS1      (int)2
#define MOTOR1_PWM1_PIN (int)21
#define MOTOR1_PWM2_PIN (int)18
#define MOTOR1_PWM3_PIN (int)14  // 14
#define MOTOR1_LIN_PINA (int)37  // CAPP
#define MOTOR1_LIN_PINB (int)35

#define MOTOR2_CS2      (int)5
#define MOTOR2_PWM1_PIN (int)25
#define MOTOR2_PWM2_PIN (int)26
#define MOTOR2_PWM3_PIN (int)27
#define MOTOR2_LIN_PINA (int)39  // VN
#define MOTOR2_LIN_PINB (int)38  // CAPN

#define MOTOR3_CS3      (int)9
#define MOTOR3_PWM1_PIN (int)22
#define MOTOR3_PWM2_PIN (int)19
#define MOTOR3_PWM3_PIN (int)23
#define MOTOR3_LIN_PINA (int)36  // VP
#define MOTOR3_LIN_PINB (int)34

#define MOTOR_SSI_SCK   (int)10
#define MOTOR_SSI_DO    (int)4

#define CAN_TXD_PIN (int)15
#define CAN_RXD_PIN (int)13

#define MOS_POWER_PIN (int)33

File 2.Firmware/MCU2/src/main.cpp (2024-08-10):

#include <SimpleFOC.h>

#include "SPI.h"
#include "bsp/can.h"
#include "comm/comm.h"
#include "comm/time.h"
#include "config/config.h"
#include "mt6701/MagneticSensorMT6701SSI.h"

using namespace Cubli::Comm;
using namespace Cubli::Bsp;

#define MOTOR_MAX_TORQUE 15.0f  // rad/s
#define MOTOR_MAX_SPEED  650   // rad/s

BLDCMotor motor1       = BLDCMotor(MOTOR_PP, MOTOR_PHASE_RESISTANCE, MOTOR_KV);
BLDCDriver3PWM driver1 = BLDCDriver3PWM(MOTOR1_PWM1_PIN, MOTOR1_PWM2_PIN, MOTOR1_PWM3_PIN);

BLDCMotor motor2       = BLDCMotor(MOTOR_PP, MOTOR_PHASE_RESISTANCE, MOTOR_KV);
BLDCDriver3PWM driver2 = BLDCDriver3PWM(MOTOR2_PWM1_PIN, MOTOR2_PWM2_PIN, MOTOR2_PWM3_PIN);

BLDCMotor motor3       = BLDCMotor(MOTOR_PP, MOTOR_PHASE_RESISTANCE, MOTOR_KV);
BLDCDriver3PWM driver3 = BLDCDriver3PWM(MOTOR3_PWM1_PIN, MOTOR3_PWM2_PIN, MOTOR3_PWM3_PIN);

 float set_ch1_motor_speed = 0;
 float set_ch2_motor_speed = 0;
 float set_ch3_motor_speed = 0;

float motor_ch1_speed;
float motor_ch2_speed;
float motor_ch3_speed;

Cubli::Bsp::MotorTransMode motor_trans_mode;

Commander command = Commander(Serial);

void CommTask(void *parameter);
void CanReceiveTask(void *parameter);
void CanSendTask(void *parameter);

float mvPa = 200 * 5.0f * 2.0f / 3.0f / 2.0f;
#define mvPa (float)200

InlineCurrentSense current_sense1 =
    InlineCurrentSense(0.0009f, mvPa, MOTOR1_LIN_PINA, MOTOR1_LIN_PINB);
InlineCurrentSense current_sense2 =
    InlineCurrentSense(0.0009f, mvPa, MOTOR2_LIN_PINA, MOTOR2_LIN_PINB);
InlineCurrentSense current_sense3 =
    InlineCurrentSense(0.0009f, mvPa, MOTOR3_LIN_PINA, MOTOR3_LIN_PINB);

float mode_control = 1;
void doMotor1(char *cmd) { command.motor(&motor3, cmd); }
void doCh1Speed(char *cmd) { command.scalar(&set_ch1_motor_speed, cmd); }
void doCh2Speed(char *cmd) { command.scalar(&set_ch2_motor_speed, cmd); }
void doCh3Speed(char *cmd) { command.scalar(&set_ch3_motor_speed, cmd); }
void doModeControl(char *cmd) { command.scalar(&mode_control, cmd); }

MagneticSensorMT6701SSI sensor1(MOTOR1_CS1);
MagneticSensorMT6701SSI sensor2(MOTOR2_CS2);
MagneticSensorMT6701SSI sensor3(MOTOR3_CS3);

SPIClass motor_spi(VSPI);
Cubli::Bsp::CanDriver can;

SemaphoreHandle_t motor_speed_semaphore;
SemaphoreHandle_t motor_set_speed_mutex;

// void setup()
// {
//     Serial.begin(115200);
//     delay(300);
//     pinMode(MOS_POWER_PIN, OUTPUT);
//     digitalWrite(MOS_POWER_PIN, LOW);

//     sensor1.init(&motor_spi);
//     sensor2.init(&motor_spi, true);
//     sensor3.init(&motor_spi, true);

//     current_sense1.init();
//     current_sense1.gain_a *= -1;

//     current_sense2.init();
//     current_sense2.gain_a *= -1;

//     current_sense3.init();
//     current_sense3.gain_a *= -1;
// }

// void loop()
// {
//     sensor1.update();
//     sensor2.update();
//     sensor3.update();
//     printf("motor1 angle: %0.3f vel: %0.3f motor2 angle: %0.3f vel: %0.3f motor3 angle: %0.3f"
//     "vel: %0.3f\r\n",
//         sensor1.getAngle(),
//         sensor1.getVelocity(),
//         sensor2.getAngle(),
//         sensor2.getVelocity(),
//         sensor3.getAngle(),
//         sensor3.getVelocity());

//     PhaseCurrent_s currents1 = current_sense1.getPhaseCurrents();
//     float current_magnitude1 = current_sense1.getDCCurrent();
//     PhaseCurrent_s currents2 = current_sense2.getPhaseCurrents();
//     float current_magnitude2 = current_sense2.getDCCurrent();
//     PhaseCurrent_s currents3 = current_sense3.getPhaseCurrents();
//     float current_magnitude3 = current_sense3.getDCCurrent();

//     // printf("motor1 a[%0.3f] mA b[%0.3f] mA c[%0.3f] mA cur[%0.3f] mA\n",
//     //     (currents1.a*-1000),
//     //     (currents1.b*1000),
//     //     (currents1.c*1000),
//     //     (current_magnitude1*1000));

//     //  printf("motor2 a[%0.3f] mA b[%0.3f] mA c[%0.3f] mA cur[%0.3f] mA\n",
//     //     (currents2.a*-1000),
//     //     (currents2.b*1000),
//     //     (currents2.c*1000),
//     //     (current_magnitude2*1000));

//     //  printf("motor3 a[%0.3f] mA b[%0.3f] mA c[%0.3f] mA cur[%0.3f] mA\n",
//     //     (currents3.a*-1000),
//     //     (currents3.b*1000),
//     //     (currents3.c*1000),
//     //     (current_magnitude3*1000));
//     delay(10);
// }

void FocInit(
    MagneticSensorMT6701SSI *sensor,
    BLDCDriver3PWM *driver,
    BLDCMotor *motor,
    InlineCurrentSense *current_sense)
{
    motor->linkSensor(sensor);
    // 驱动器设置
    driver->voltage_power_supply = 11.1;
    driver->init();
    motor->linkDriver(driver);

    current_sense->linkDriver(driver);
    current_sense->init();

    current_sense->gain_a *= -1;
    motor->linkCurrentSense(current_sense);

    motor->torque_controller = TorqueControlType::foc_current;
    motor->controller        = MotionControlType::torque;
    motor->motion_downsample = 0.0;

    // velocity loop PID
    motor->PID_velocity.P           = 1.0;
    motor->PID_velocity.I           = 20.0;
    motor->PID_velocity.D           = 0.0;
    motor->PID_velocity.output_ramp = 1000.0;
    motor->PID_velocity.limit       = 2.5;
    // Low pass filtering time constant
    motor->LPF_velocity.Tf = 0.005;

    // angle loop PID
    motor->P_angle.P           = 20.0;
    motor->P_angle.I           = 0.0;
    motor->P_angle.D           = 0.0;
    motor->P_angle.output_ramp = 0.0;
    motor->P_angle.limit       = 20.0;
    // Low pass filtering time constant
    motor->LPF_angle.Tf = 0.0;
    // current q loop PID
    motor->PID_current_q.P           = 0.5;
    motor->PID_current_q.I           = 50.0;  // 20
    motor->PID_current_q.D           = 0.0;
    motor->PID_current_q.output_ramp = 0.0;
    motor->PID_current_q.limit       = 0.85f;
    // Low pass filtering time constant
    motor->LPF_current_q.Tf = 0.002;
    // current d loop PID
    motor->PID_current_d.P           = 0.5;
    motor->PID_current_d.I           = 50.0;  // 50
    motor->PID_current_d.D           = 0.0;
    motor->PID_current_d.output_ramp = 0.0;
    motor->PID_current_d.limit       = 0.85;
    // Low pass filtering time constant
    motor->LPF_current_d.Tf = 0.005;
    // Limits
    motor->velocity_limit = 20.0;
    motor->voltage_limit  = 3.5f;  // 数字电源：3.0 电池：3.5
    motor->current_limit  = 3.5f;

    motor->useMonitoring(Serial);

    motor->monitor_downsample = 0;
    motor->monitor_variables  = _MON_TARGET | _MON_VEL | _MON_ANGLE | _MON_CURR_Q;

    // 电机初始化
    motor->init();
    motor->initFOC();
}
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

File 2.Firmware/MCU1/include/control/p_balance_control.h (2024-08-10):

#pragma once

#include "comm/comm.h"
#include "control/angle_offset_calibration.h"
#include "control/control_base.h"

namespace CubliMini {
namespace Control {

#define P_BALABCE_PROTECTION_THRESHOLD 20
#define P_BALABCE_OUTPUT_LIMIT         15

class PBalanceControl
{
   public:
    struct PAxisParam
    {
        AxisParam_t x;
        AxisParam_t y;
        AxisParam_t z;
    };

    struct PSensor
    {
        AxisSensor_t x;
        AxisSensor_t y;
        AxisSensor_t z;
    };

    struct MotorSpeed
    {
        float ch1;
        float ch2;
        float ch3;
        uint8_t value;
        uint8_t control_mode;
    };

    struct AxisSpeed
    {
        float x;
        float y;
        float z;
    };

    using AxisControl  = AxisSpeed;
    using MotorControl = MotorSpeed;

    PBalanceControl(PAxisParam &lqr_param, float &cal_angle_kp)
        : lqr_param_(lqr_param),
          cube_is_upside_dowm_(false),
          output_limit_(P_BALABCE_OUTPUT_LIMIT),
          angle_protection_threahold_(P_BALABCE_PROTECTION_THRESHOLD),
          x_angle_offset_auto_cal_(cal_angle_kp),
          y_angle_offset_auto_cal_(cal_angle_kp)
    {}

    MotorControl Loop(PSensor &sensor, const MotorSpeed &motor_speed, bool is_static, float yaw_control)
    {
        MotorControl motor_control = {0, 0, 0};
        if (is_static)
        {
            cube_is_upside_dowm_ = false;
        }

        if (fabs(sensor.x.angle - lqr_param_.x.angle_offset) < fabs(angle_protection_threahold_) &&
            fabs(sensor.y.angle - lqr_param_.y.angle_offset) < fabs(angle_protection_threahold_) &&
            cube_is_upside_dowm_ == false)
        {
            AxisSpeed axis_speed;
            GetAxisMoveSpeed(motor_speed, axis_speed);
            sensor.x.speed = axis_speed.x;
            sensor.y.speed = axis_speed.y;
            sensor.z.speed = axis_speed.z;

            AxisControl axis_control;
            axis_control.x = AxisLqr(sensor.x, lqr_param_.x);
            axis_control.y = AxisLqr(sensor.y, lqr_param_.y);
            axis_control.z = AxisLqr(sensor.z, lqr_param_.z) + yaw_control;
            GetMotorMoveSpeed(axis_control, motor_control);

            x_angle_offset_auto_cal_.Loop(-axis_speed.x, lqr_param_.x.angle_offset, is_static, sensor.x.angle);
            // y_angle_offset_auto_cal_.Loop(-axis_speed.y, lqr_param_.y.angle_offset, is_static, sensor.y.angle);
        }
        else
        {
            motor_control.ch1    = 0;
            motor_control.ch2    = 0;
            motor_control.ch3    = 0;
            cube_is_upside_dowm_ = true;
        }

        motor_control.ch1 = Comm::Limit(motor_control.ch1, output_limit_);
        motor_control.ch2 = Comm::Limit(motor_control.ch2, output_limit_);
        motor_control.ch3 = Comm::Limit(motor_control.ch3, output_limit_);
        return motor_control;
    }

   private:
    void GetAxisMoveSpeed(const MotorSpeed &_get_speed, AxisSpeed &_axis_speed)
    {
        _axis_speed.x = _get_speed.ch2 - _get_speed.ch3 * sin((30) / 57.3f) -
                        _get_speed.ch1 * sin((30) / 57.3f);
        _axis_speed.y = (_get_speed.ch3 - _get_speed.ch1) * cos((30) / 57.3f);
        _axis_speed.z = (_get_speed.ch2 + _get_speed.ch3 + _get_speed.ch1);
    }

    void GetMotorMoveSpeed(const AxisControl &axis_control, MotorControl &motor_control)
    {
        motor_control.ch1 = -axis_control.y * cos((30) / 57.3f) -
                            axis_control.x * sin((30) / 57.3f) + axis_control.z / 3.0f;
        motor_control.ch2 = axis_control.x + axis_control.z / 3.0f;
        motor_control.ch3 = -axis_control.x * sin((30) / 57.3f) +
                            axis_control.y * cos((30) / 57.3f) + axis_control.z / 3.0f;
    }

   public:
    PAxisParam &lqr_param_;
    float output_limit_;
    float angle_protection_threahold_;
    AngleOffsetCalibration x_angle_offset_auto_cal_;
    AngleOffsetCalibration y_angle_offset_auto_cal_;

   private:
    bool cube_is_upside_dowm_;
};

}  // namespace Control
}  // namespace CubliMini

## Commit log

2024-08-11 feat: 1.添加刹车片的图纸 2.修正bom的灯罩的数量
    [Cubli_Mini_Ultra BOM.xlsx, 刹车片.DWG, 刹车片.STEP]
2024-08-31 bugfix: vofa+增加对应的命令
2024-10-18 feat: 1. 添加主控板的PCB生产文件和原理图 2. BOM添加LED光污染购买链接和型号
    [BOM_main_main_2024-10-18.xlsx, Cubli_Mini_Ultra BOM.xlsx, PickAndPlace_main_2024-10-18.xlsx]
